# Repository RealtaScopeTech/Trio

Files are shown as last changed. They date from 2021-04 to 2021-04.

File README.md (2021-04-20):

# Trio
Realta Scope Tech: Trio Focuser

# What is it?

The REALTA Trio is a device that can control dew heaters, distribute 12 volt power and is an ASCOM compatible focuser. 

# Why did you make it?

The cost of some auxiliary astronomy equipment is crazy. I had no intention of paying $100 for a device the controls dew heaters via simple pulse width modulation, another $100 on a box that connects red and black wires to distribute 12v power and $200+ on a focuser controller. The cost saving plus the potential to learn something really intrigued me and the amount of information/free tools and general advice available to help people make things really inspired me, it's just astounding how useful the internet and open source/hardware have become. 

I also wanted to design something that fitted in a neat case as other maker options had a distinct DIY look to them, I wanted something that looked finished.

# License

Please feel free to make your own copies of the board/cases and ammend their design. Please give credit.

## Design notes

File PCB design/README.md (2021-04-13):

# PCB Design

The files used to design the PCB can be found in the KiCAD folder.

You may get issues with KiCAD not being able to find custom footprints and 3D models. We have placed all of those used within the KiCAD Extra's folder.

The "Production Files" folder contains all the files need to manufacture the PCB. It includes the Gerber files and a SMD position file and BOM file that can be used with JLCPCB to manufature a board with the SMD components included.

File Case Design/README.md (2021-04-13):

# Case Design

FreeCAD source files and STL's.

The parts are designed to be printed without supports. The motorhousing can be succesfully printed from the side which covers the stepper motors wires.

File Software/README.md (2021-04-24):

# Software
Realta Scope Tech: Trio Focuser

Windows Drivers => Contains drivers for the USB to Serial hardware found on many common Arduino Nano clones.

Select the folder that matches the name of the stepper driver board you are using in your Realta: Trio.

The installation process is the same for each driver.

# Nano software isntall

1) If needed install the driver for your Arduino's USB to Serial hardware.
2) Download the Arduino source code that matches your Arduino modela and the Stepper driver board you are using.
3) Download and install the Arduino IDE.
4) In the Arduino IDE install Adafruits AHT libraries.
5) Plug your Nano in
6) Open the Ardunio sketch source code you downloaded and compile/uploade it to the Nano.

# Windows app

1) Download the Trio.exe
2) Copy it somewhere where you can find it again!
3) Double click to run

# ASCOM driver.

1) Download the installer RealtaTrioASCOMSetup.exe, this is unsigned so Windows will probably think its a virus and warn you not to install it.

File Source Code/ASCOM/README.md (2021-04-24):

# ASCOM driver source code

Visual studio files

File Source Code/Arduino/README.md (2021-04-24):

# Arduniuo source code

Please select the approriate sketch for your stepper driver

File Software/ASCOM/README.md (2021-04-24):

# ASCOM

This ASCOM driver allows the focuser to be controlled with other ASCOM compliant software. 

It can not be used at the same time as the Windows desktop standalone app.

Dew controllers can be changed via the focusers settings menu.

Please note the driver is unsigned, Windows will therefore likely decide that it's a virus! You will need to select the option to install anyway.

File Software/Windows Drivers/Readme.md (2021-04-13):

# Windows Drivers
Drivers for Nano Clones USB to Serial hardware.

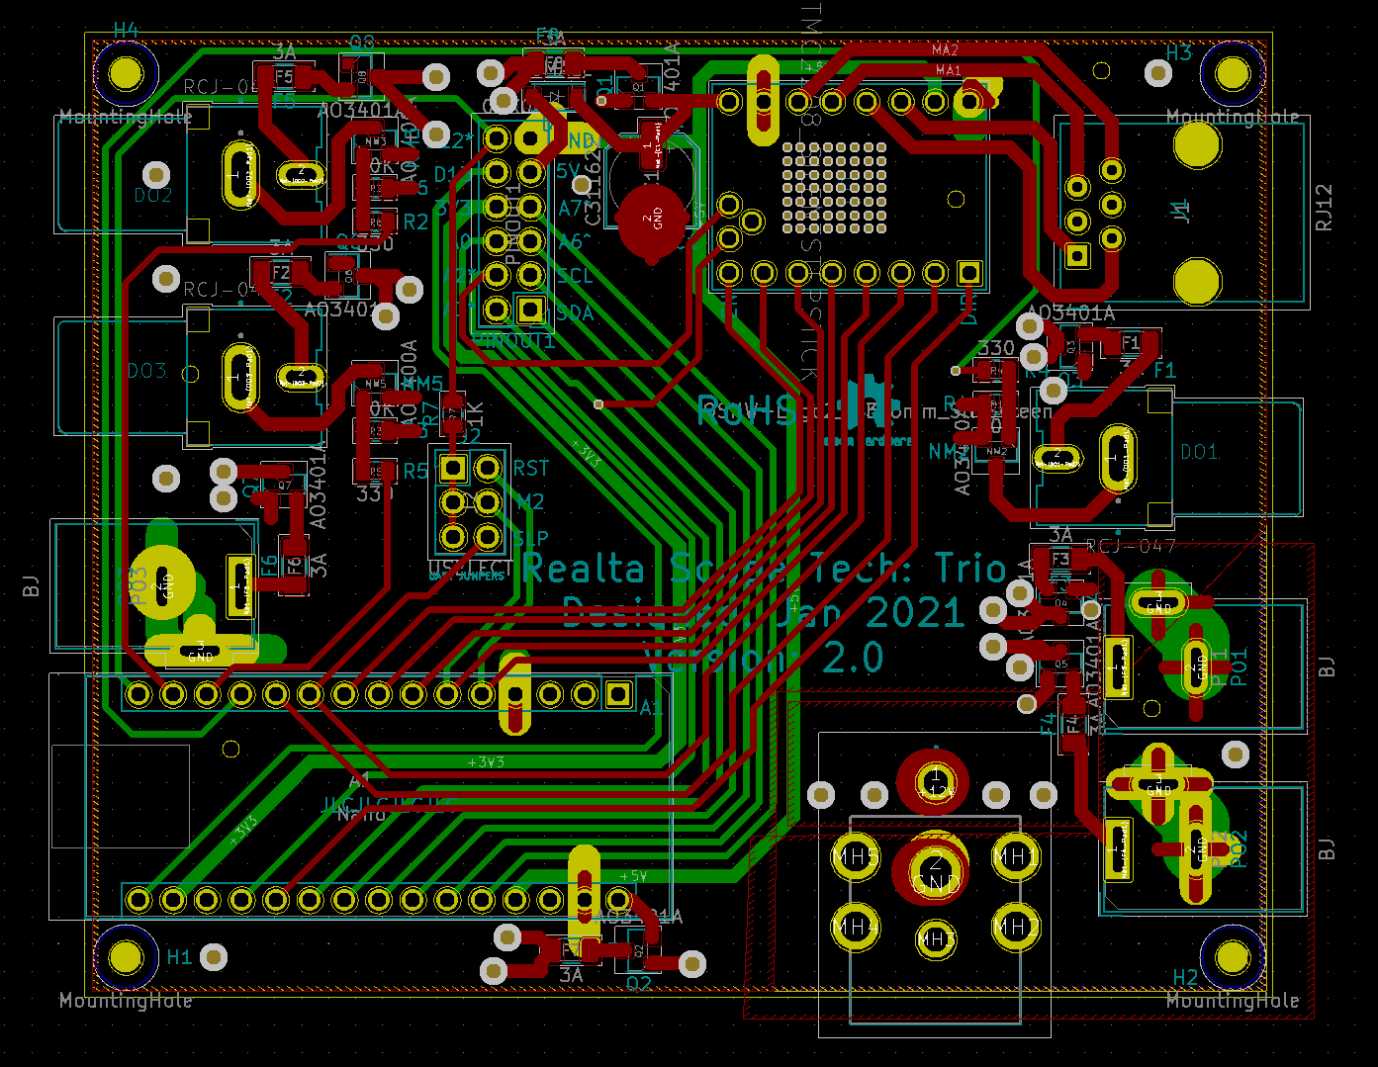
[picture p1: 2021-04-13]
PCB design/PCBLayout.png

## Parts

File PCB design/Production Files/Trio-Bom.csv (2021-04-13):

Comment | Designator | Footprint | LCSC
C311622 | C1 | Capacitor_SMD:CP_Elec_6.3x7.7 | C311622
DSMALL | D1 | Diode_SMD:D_SOD-123 | C8598
3A | F1,F2,F3,F4,F5,F6,F7,F8 | Fuse:Fuse_1206_3216Metric | C182445
AO3400A | NM2,NM3,NM5 | Package_TO_SOT_SMD:SOT-23 | C20917
AO3401A | Q1,Q2,Q3,Q4,Q5,Q6,Q7,Q8 | Package_TO_SOT_SMD:SOT-23 | C15127
10K | R1,R2,R3 | Resistor_SMD:R_0805_2012Metric | C17414
330 | R4,R5,R6 | Resistor_SMD:R_0805_2012Metric | C17630
1K | R7 | Resistor_SMD:R_0805_2012Metric | C17513

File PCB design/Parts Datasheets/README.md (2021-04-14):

# Parts Datasheets

Here you can find the data sheets of all the parts used in the Realta: Trio

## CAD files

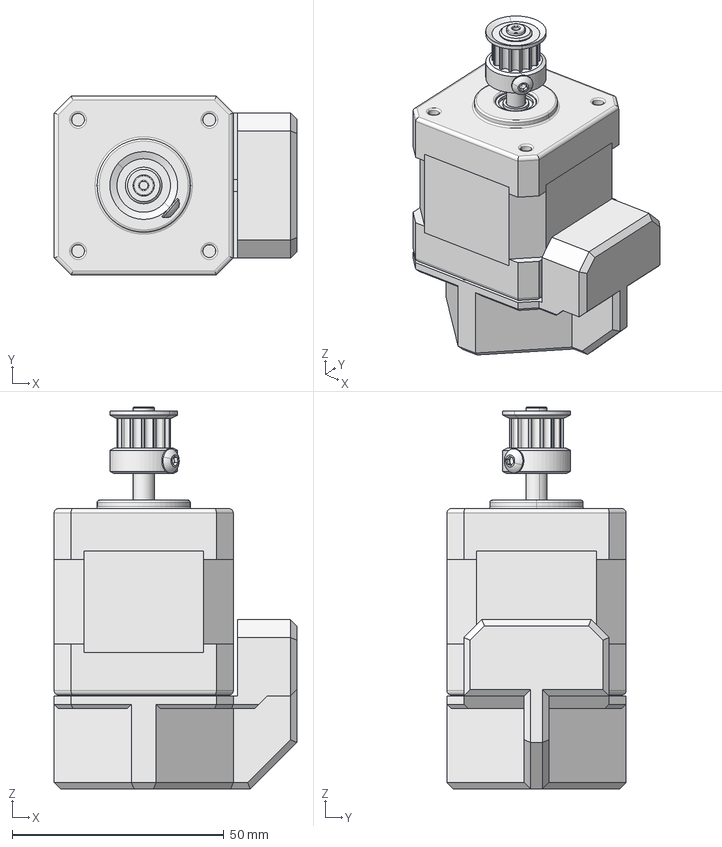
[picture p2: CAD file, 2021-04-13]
Case Design/FreeCAD/TrioMotorHousing.FCStd
57.3 x 42.3 x 90.2 mm
Base
Cuerpo
Tapa
pan cross head_am_B18.6.7M - M3 x 0.5 x 5 Type I Cross Recessed PHMS --5N
pan cross head_am_B18.6.7M - M3 x 0.5 x 5 Type I Cross Recessed PHMS --5N001
pan cross head_am_B18.6.7M - M3 x 0.5 x 5 Type I Cross Recessed PHMS --5N002
pan cross head_am_B18.6.7M - M3 x 0.5 x 5 Type I Cross Recessed PHMS --5N003
Eje
instrument ball bearing_68_am_AFBMA 12.1.4.1 - 0050-11 - 10,SI,NC,10_68
instrument ball bearing_68_am_AFBMA 12.1.4.1 - 0050-11 - 10,SI,NC,10_069
socket button head cap screw_am_B18.3.4M - 3 x 0.5 x 5 SBHCS --N
T5 Pulley

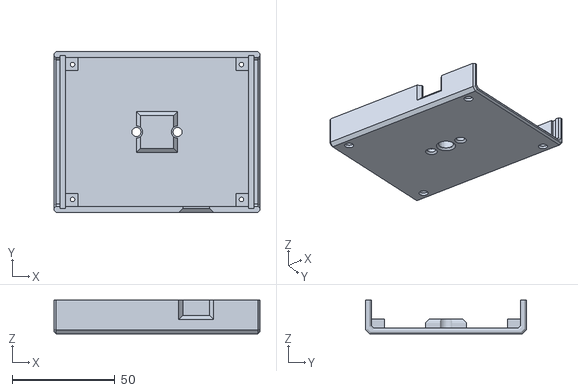
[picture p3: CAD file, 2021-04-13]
Case Design/STL/TrioLoweCase.stl
100.0 x 78.1 x 16.5

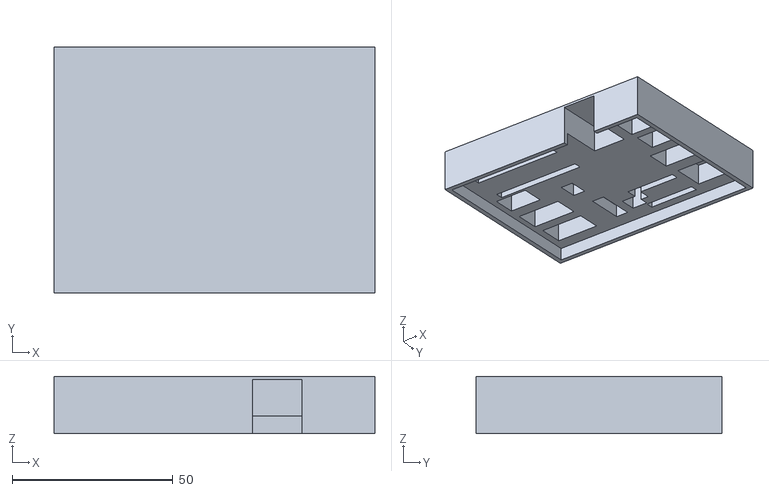
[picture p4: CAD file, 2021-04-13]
Case Design/STL/PCBSolderJig.stl
100.0 x 76.6 x 17.8

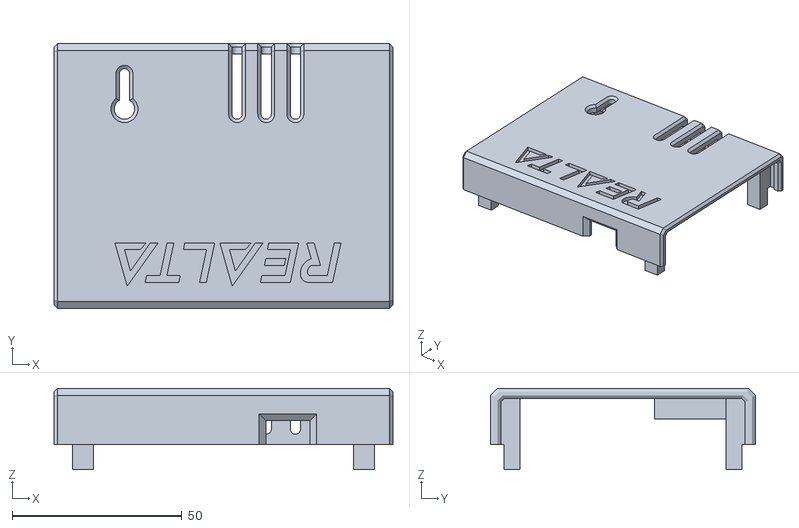
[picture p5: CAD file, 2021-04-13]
Case Design/STL/TrioUpperCase.stl
100.0 x 78.1 x 23.9

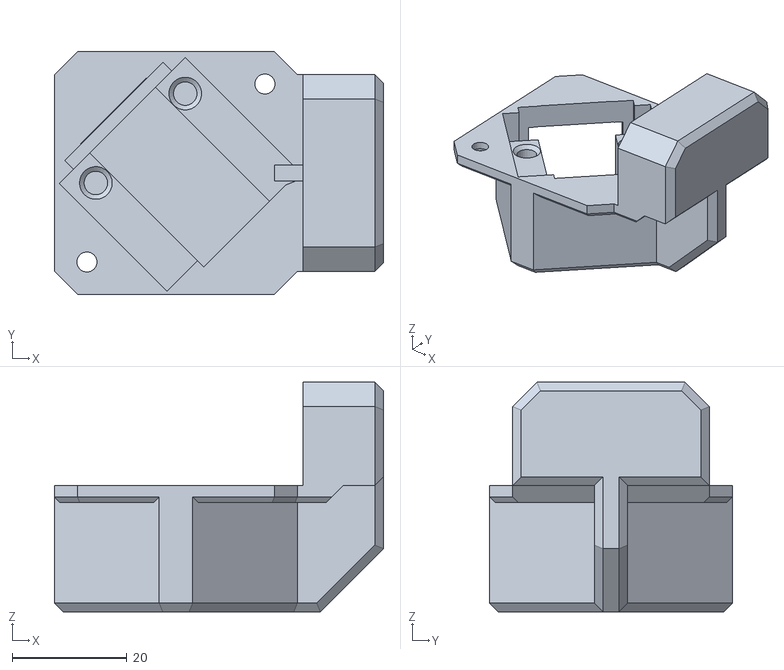
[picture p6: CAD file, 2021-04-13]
Case Design/STL/MotorHousing.stl
57.3 x 42.3 x 40.0

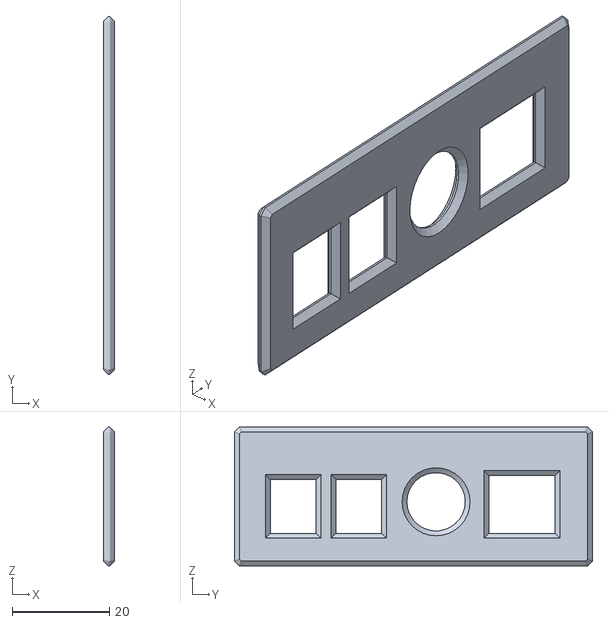
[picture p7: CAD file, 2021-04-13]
Case Design/STL/TrioFacePlateA.stl
2.32 x 73.7 x 28.6

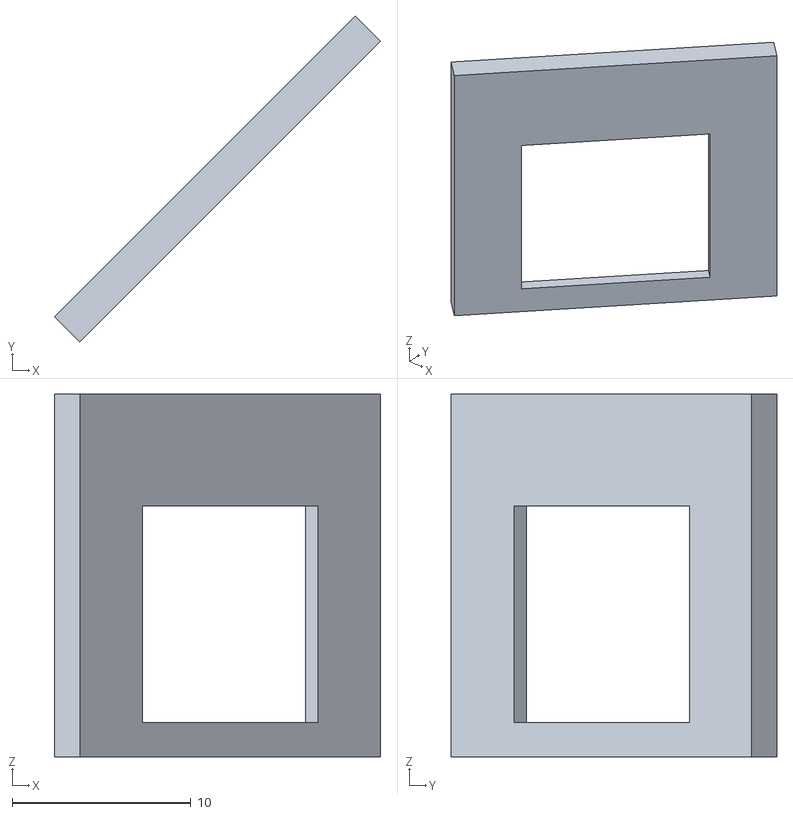
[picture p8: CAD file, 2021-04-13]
Case Design/STL/MotorFacePlate.stl
18.2 x 18.2 x 20.3

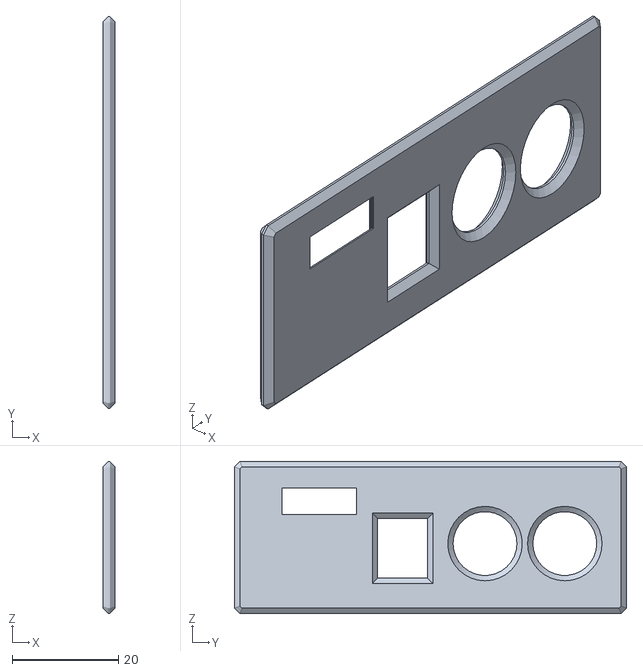
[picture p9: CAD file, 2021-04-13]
Case Design/STL/TrioFacePlateB.stl
2.32 x 73.7 x 28.6

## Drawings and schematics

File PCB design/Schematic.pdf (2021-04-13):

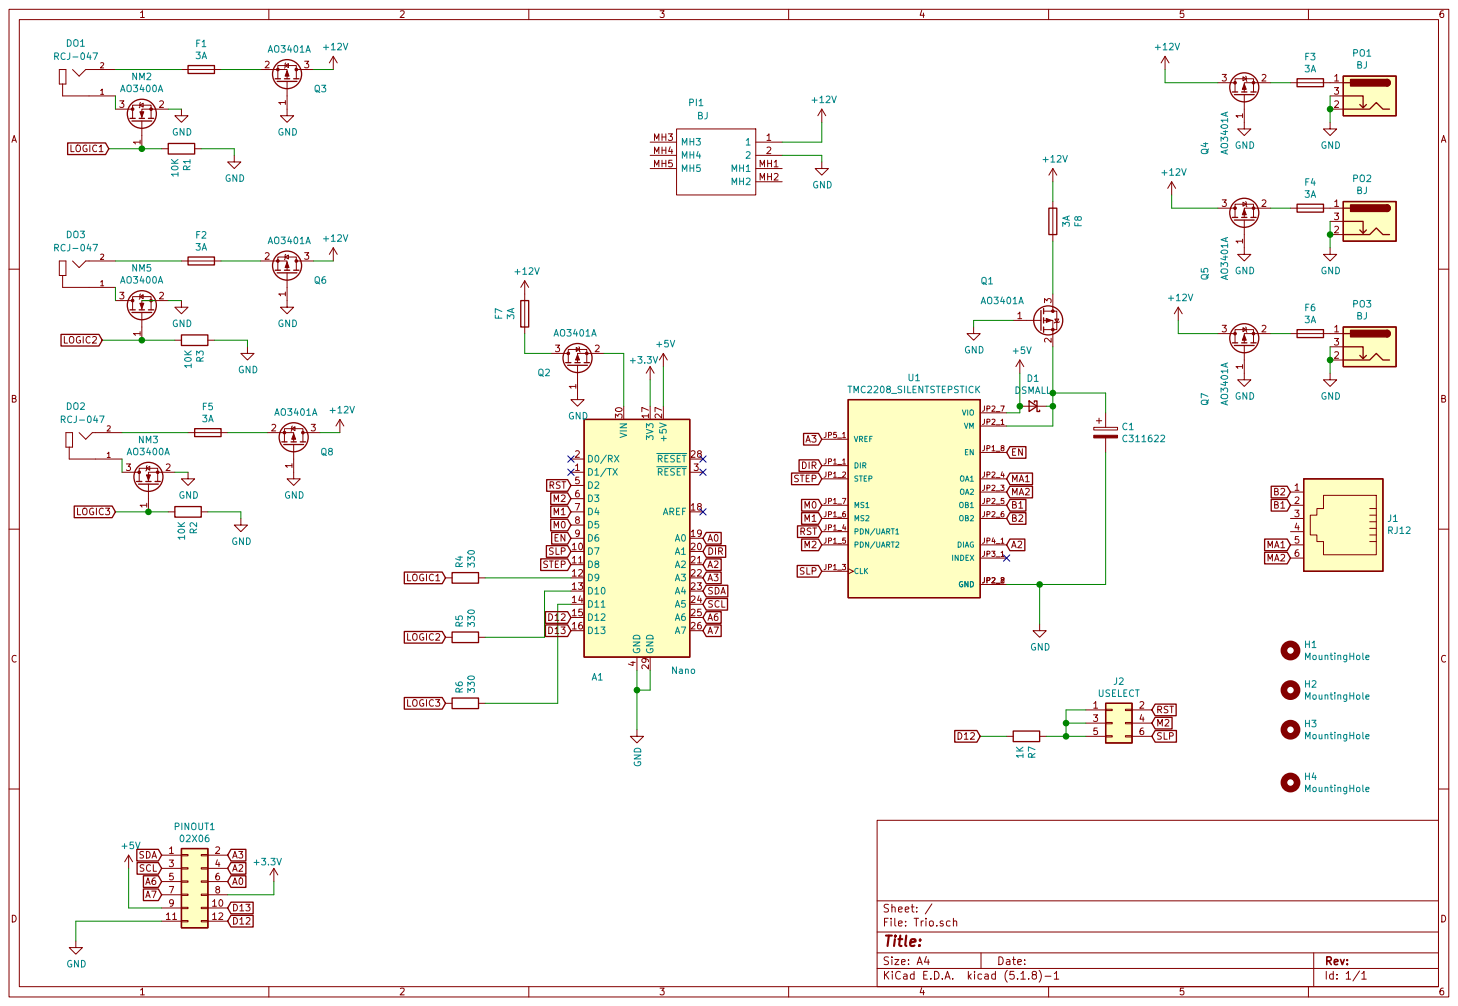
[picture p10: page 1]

Id: 1/1 Title: File: Trio.sch Sheet: / +3.3V

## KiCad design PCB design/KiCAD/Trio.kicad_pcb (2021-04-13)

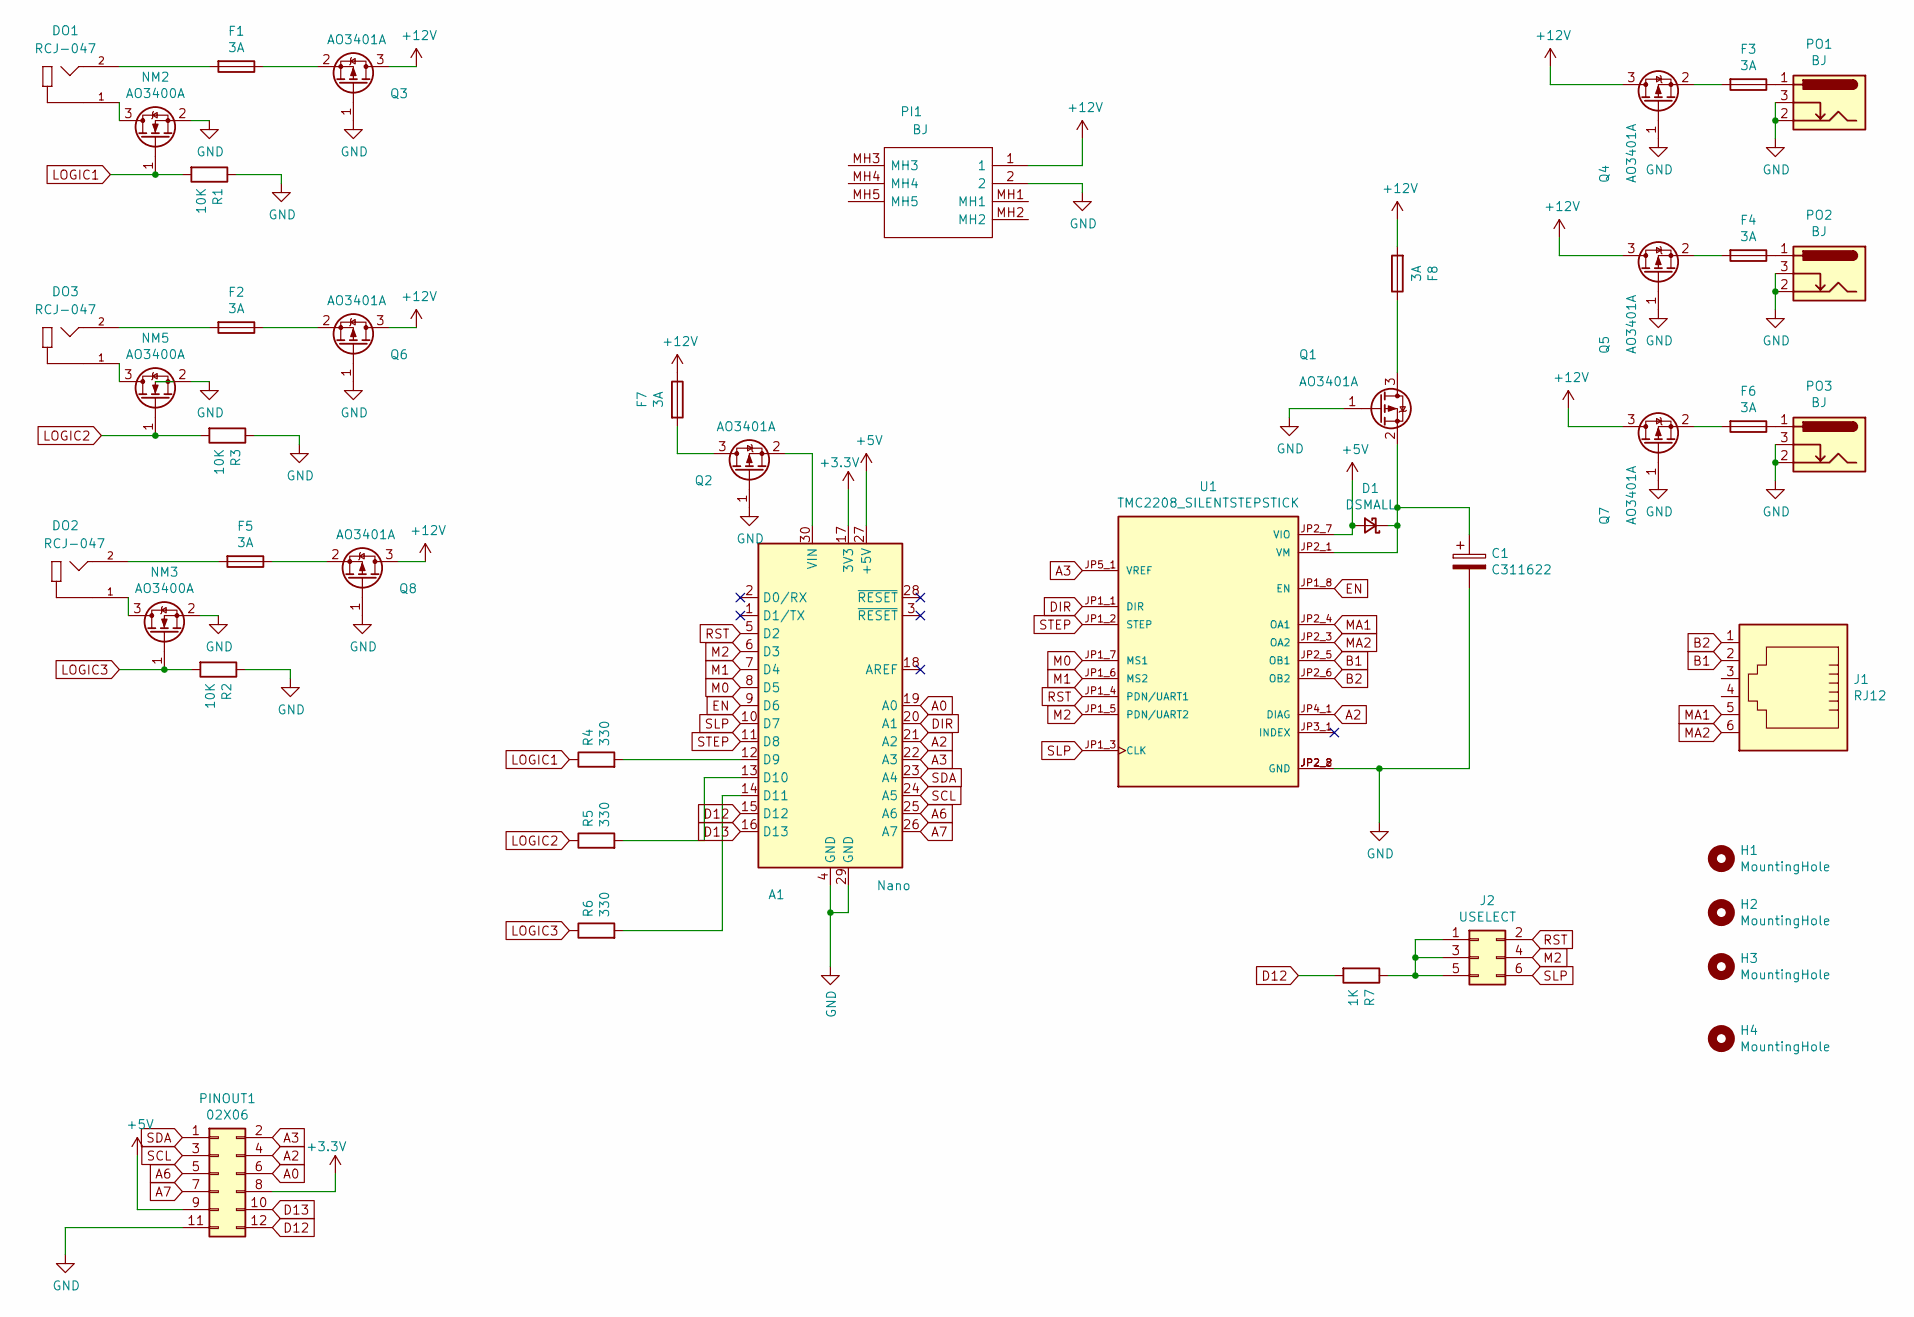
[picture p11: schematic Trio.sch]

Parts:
A1: Nano; Arduino_Nano
C1: C311622; CP_Elec_6.3x7.7; LCSC Part # C311622
D1: DSMALL; D_SOD-123; LCSC Part # C8598
DO1, DO2, DO3: RCJ-047; CUI_RCJ-047
F1, F2, F3, F4, F5, F6, F7, F8: 3A; Fuse_1206_3216Metric; LCSC Part # C182445
H1, H2, H3, H4: MountingHole; MountingHole_2.2mm_M2
J1: RJ12; RJ12_Amphenol_54601
J2: USELECT; PinHeader_2x03_P2.54mm_Vertical
NM2, NM3, NM5: AO3400A; SOT-23; LCSC Part # C20917
PI1: BJ; FC681495
PINOUT1: 02X06; PinHeader_2x06_P2.54mm_Vertical
PO1, PO2, PO3: BJ; BarrelJack_Wuerth_6941xx301002
Q1, Q2, Q3, Q4, Q5, Q6, Q7, Q8: AO3401A; SOT-23; LCSC Part # C15127
R1, R2, R3: 10K; R_0805_2012Metric; LCSC Part # C17414
R4, R5, R6: 330; R_0805_2012Metric; LCSC Part # C17630
R7: 1K; R_0805_2012Metric; LCSC Part # C17513
U1: TMC2208_SILENTSTEPSTICK; MODULE_TMC2208_SILENTSTEPSTICK; PARTREV v11

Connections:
+3V3: A1.17 (3V3), PINOUT1.8
+5V: A1.27 (+5V), D1.2 (A), PINOUT1.9, U1.JP2_7 (VIO)
+12V: F7.1, F8.2, PI1.1, Q3.3 (D), Q4.3 (D), Q5.3 (D), Q6.3 (D), Q7.3 (D), Q8.3 (D)
A0: A1.19 (A0), PINOUT1.6
A2: A1.21 (A2), PINOUT1.4, U1.JP4_1 (DIAG)
A3: A1.22 (A3), PINOUT1.2, U1.JP5_1 (VREF)
A6: A1.25 (A6), PINOUT1.5
A7: A1.26 (A7), PINOUT1.7
B1: J1.2, U1.JP2_5 (OB1)
B2: J1.1, U1.JP2_6 (OB2)
D12: A1.15 (D12), PINOUT1.12, R7.2
D13: A1.16 (D13), PINOUT1.10
DIR: A1.20 (A1), U1.JP1_1 (DIR)
EN: A1.9 (D6), U1.JP1_8 (EN)
GND: A1.4 (GND), A1.29 (GND), C1.2, NM2.2 (S), NM3.2 (S), NM5.2 (S), PI1.2, PINOUT1.11, PO1.2, PO1.3, PO2.2, PO2.3, PO3.2, PO3.3, Q1.1 (G), Q2.1 (G), Q3.1 (G), Q4.1 (G), Q5.1 (G), Q6.1 (G), Q7.1 (G), Q8.1 (G), R1.1, R2.1, R3.1, U1.JP2_2 (GND), U1.JP2_8 (GND)
LOGIC1: NM2.1 (G), R1.2, R4.1
LOGIC2: NM5.1 (G), R3.2, R5.1
LOGIC3: NM3.1 (G), R2.2, R6.1
M0: A1.8 (D5), U1.JP1_7 (MS1)
M1: A1.7 (D4), U1.JP1_6 (MS2)
M2: A1.6 (D3), J2.4, U1.JP1_5 (PDN/UART2)
MA1: J1.5, U1.JP2_4 (OA1)
MA2: J1.6, U1.JP2_3 (OA2)
unnamed: A1.12 (D9), R4.2
unnamed: A1.13 (D10), R5.2
unnamed: A1.14 (D11), R6.2
unnamed: A1.30 (VIN), Q2.2 (S)
unnamed: C1.1, D1.1 (K), Q1.2 (S), U1.JP2_1 (VM)
unnamed: DO1.1, NM2.3 (D)
unnamed: DO1.2, F1.2
unnamed: DO2.1, NM3.3 (D)
unnamed: DO2.2, F5.2
unnamed: DO3.1, NM5.3 (D)
unnamed: DO3.2, F2.2
unnamed: F1.1, Q3.2 (S)
unnamed: F2.1, Q6.2 (S)
unnamed: F3.1, PO1.1
unnamed: F3.2, Q4.2 (S)
unnamed: F4.1, PO2.1
unnamed: F4.2, Q5.2 (S)
unnamed: F5.1, Q8.2 (S)
unnamed: F6.1, PO3.1
unnamed: F6.2, Q7.2 (S)
unnamed: F7.2, Q2.3 (D)
unnamed: F8.1, Q1.3 (D)
unnamed: J2.1, J2.3, J2.5, R7.1
RST: A1.5 (D2), J2.2, U1.JP1_4 (PDN/UART1)
SCL: A1.24 (A5), PINOUT1.3
SDA: A1.23 (A4), PINOUT1.1
SLP: A1.10 (D7), J2.6, U1.JP1_3 (CLK)
STEP: A1.11 (D8), U1.JP1_2 (STEP)

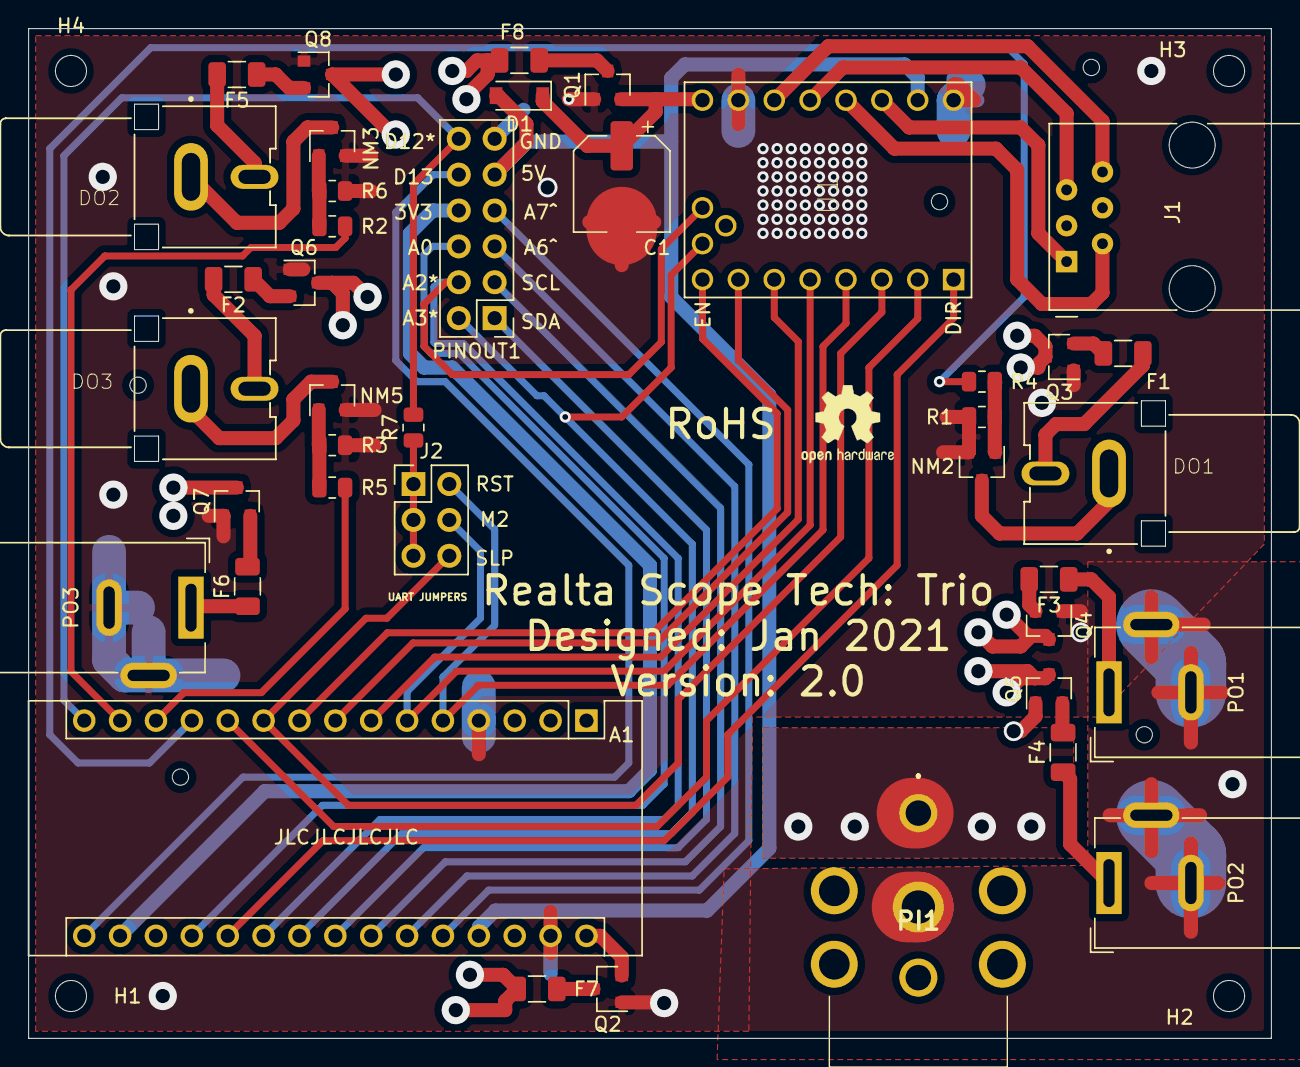
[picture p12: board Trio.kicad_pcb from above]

Board: 4 copper layers, 88.0 x 71.5 mm, 44 parts (0 on the bottom side), 51 nets.

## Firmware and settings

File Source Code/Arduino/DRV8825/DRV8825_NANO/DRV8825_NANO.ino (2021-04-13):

// Realta: Súil a Trí
#include <EEPROM.h>
#include <Arduino.h>
#include <Adafruit_AHTX0.h>
#include "MyData.h"
#include "MyEPROM.h"
#include "MyDew.h"
#include "MyFocus.h"
#include "MyTemp.h"
#include "MySerial.h"

void setup() {
  // turn the serial port on
  // code in MySerial.h
  P_INIT_SERIAL_PORT();
  
  // Set output pins
  // See DataStructure for pin mapping
  // Code in MyData.h
  P_SET_OUTPUT_PINS();
  
  //Read last saved dew status
  // Code in MyEPROM.h
  READ_EPROM_DEW();
  
  //Read last saved dew status
  // Code in MyEPROM.h
  READ_EPROM_FOCUSER();
  //Set PWM values to zero
  //We do not want these to come on unless user asks for it
  V_DEW_LOCKED = true;
  V_IS_MOVING = false;
  V_STEPS_TO_MAKE = 0;

  // SET DEFAULT STEPPING MODE REFERENCES
  P_SET_STEPPING_MODES();

  // SET SLEEP AND RESET HIGH
  pinMode(2, OUTPUT);
  pinMode(7, OUTPUT);
  digitalWrite(2, HIGH );
  digitalWrite(7, HIGH );

  // UPDATE STEPPING PINS TO SAVED VALUES
  P_UPDATE_STEPPER_PINS();

  // Try to start AHT20
  P_CHECK_SENSOR_EXISTS();

  // Read temp offset
  READ_EPROM_TEMP_OFFSET();
  
}


//////////////////////////////////////////////////////////////////////
//////////////////////////////////////////////////////////////////////
//////////////////////////////////////////////////////////////////////
//////////////////////////////////////////////////////////////////////


void loop() {
  
  ////////////////////////////////
  //
  // Check and read serial port
  //
  ///////////////////////////////

  // This procedure reads latest serial port 
  // value and decides what to do with it
  // it will keep adding chars to V_SERIAL_TEXT until it gets to a line feed
  // then send the command on to processing
  // Code in MySerial.h
  P_PROCESS_SERIAL_PORT ();

  if (V_IS_MOVING)
  {
    P_STEP ();
  }

  // Not sure if I need to keep setting the PWM pins every loop.
  // Code in MyDew.h
  P_SET_PWM_PINS();

}

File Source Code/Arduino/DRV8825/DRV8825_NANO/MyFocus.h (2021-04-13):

/*
byte DEW_0_PIN = 9;       //PWM PULSES
byte DEW_1_PIN = 10;      //PWM PULSES
byte DEW_2_PIN = 11;      //PWM PULSES
byte STEP_DIR_PIN = 3;    //SETS DIRECTION
byte STEP_STEP_PIN = 4;   //TELLS MOTOR TO MOVE
byte STEP_ENABLE_PIN = 8; //ENABLES POWER TO MOTOR
byte STEP_M3_PIN = 7;     //FOR SETTING STEP SIZE
byte STEP_M2_PIN = 6;     //FOR SETTING STEP SIZE
byte STEP_M1_PIN = 5;     //FOR SETTING STEP SIZE

struct FOCUSER_STATUS {
  int  V_CURRENT_POSITION;
  byte V_STEP_MODE;
  int  V_MAX_STEPS;
  byte V_POWER_HOLD;
  byte V_DIRECTTION;
  byte V_STEPPER_SPEED;
};

*/

// STEPPER CONTROL

void P_UPDATE_STEPPER_PINS()
{
digitalWrite(STEP_DIR_PIN, S_MY_FOCUSER_STATUS.V_DIRECTTION);
digitalWrite(STEP_ENABLE_PIN, S_MY_FOCUSER_STATUS.V_POWER_HOLD);
digitalWrite(STEP_M1_PIN, STEPPING_MODE[S_MY_FOCUSER_STATUS.V_STEP_MODE].M1_STATE );
digitalWrite(STEP_M2_PIN, STEPPING_MODE[S_MY_FOCUSER_STATUS.V_STEP_MODE].M2_STATE );
digitalWrite(STEP_M3_PIN, STEPPING_MODE[S_MY_FOCUSER_STATUS.V_STEP_MODE].M3_STATE );
}

// SERIAL LETTER 'FOCUSER_GET_STATUS': GET_FOCUSER_STATUS
//  returns
//  V_CURRENT_POSITION, V_STEP_MODE, V_MAX_STEPS, V_POWER_HOLD, V_DIRECTTION, V_STEPPER_SPEED;
//  return should look like GET_STEPPER_STATUS|5000, 1, 10000, 0, 0, 1

// SERIAL LETTER 'D': SET_STEPPER_STATUS
// sends new V_CURRENT_POSITION, V_STEP_MODE, V_MAX_STEPS, V_POWER_HOLD, V_DIRECTTION, V_STEPPER_SPEED;

// SERIAL 'FOCUSER_MOVE': MOVE_NUMBER_OF_STEPS
void P_OUTPUT_FOCUSER_STATUS ()
{
  V_SERIAL_OUT ="";

   V_SERIAL_OUT = "FOCUSER_STATUS";
   V_SERIAL_OUT = V_SERIAL_OUT + "|";
   V_SERIAL_OUT = V_SERIAL_OUT + S_MY_FOCUSER_STATUS.V_CURRENT_POSITION + "," ; 
   V_SERIAL_OUT = V_SERIAL_OUT + S_MY_FOCUSER_STATUS.V_STEP_MODE + ","; 
   V_SERIAL_OUT = V_SERIAL_OUT + S_MY_FOCUSER_STATUS.V_MAX_STEPS + "," ;
   V_SERIAL_OUT = V_SERIAL_OUT + S_MY_FOCUSER_STATUS.V_POWER_HOLD + "," ;
   V_SERIAL_OUT = V_SERIAL_OUT + S_MY_FOCUSER_STATUS.V_DIRECTTION + "," ;
   V_SERIAL_OUT = V_SERIAL_OUT + S_MY_FOCUSER_STATUS.V_STEPPER_SPEED + ",";
   V_SERIAL_OUT = V_SERIAL_OUT + S_MY_FOCUSER_STATUS.V_STEPPER_WAIT;
   Serial.println(V_SERIAL_OUT);
   
};  

void P_STEP ()
{
    if(V_STEPS_TO_MAKE != 0)
    {
    // We will update stepper pins to users last settings
    P_UPDATE_STEPPER_PINS();

    // We will ignore enable flag because we do actually want to move
    digitalWrite(STEP_ENABLE_PIN, LOW);

   // Reverse direction if negative steps
    if (V_STEPS_TO_MAKE < 0)
    {
    if(S_MY_FOCUSER_STATUS.V_DIRECTTION == 1)
      {
        digitalWrite(STEP_DIR_PIN, 0);
      }
      else
      {
        digitalWrite(STEP_DIR_PIN, 1);
      }
    }
    
    delay(S_MY_FOCUSER_STATUS.V_STEPPER_SPEED); // Wait per user speed delay
    // Focuser moves only when stop pin changes from high to low
    digitalWrite(STEP_STEP_PIN, LOW);
    digitalWrite(STEP_STEP_PIN, HIGH) ;
      
    // Wait for it   
    delay(S_MY_FOCUSER_STATUS.V_STEPPER_WAIT);  

    if (V_STEPS_TO_MAKE < 0)
    {
    S_MY_FOCUSER_STATUS.V_CURRENT_POSITION = S_MY_FOCUSER_STATUS.V_CURRENT_POSITION - 1;
    V_STEPS_TO_MAKE =  V_STEPS_TO_MAKE + 1;
    }
    else
    {
    S_MY_FOCUSER_STATUS.V_CURRENT_POSITION = S_MY_FOCUSER_STATUS.V_CURRENT_POSITION + 1;
    V_STEPS_TO_MAKE =  V_STEPS_TO_MAKE - 1;   
    }
    }

    // Output progress
    if (V_STEPS_TO_MAKE % 100 == 0)
    {
    Serial.print("MOVING|"); Serial.println(V_STEPS_TO_MAKE);
    }


    if (V_STEPS_TO_MAKE==0)
    {
    V_IS_MOVING = false;
    SAVE_EPROM_FOCUSER();
    P_OUTPUT_FOCUSER_STATUS ();
    }
    
    // We will update stepper pins back to user settings 
    P_UPDATE_STEPPER_PINS();
    
}


void P_MOVE_FOCUSER ()
{
   // We expect parameter containing number of steps
   // throw error back if we don't have any
   if(!V_HAS_PARAMS) 
   {
      Serial.println ("ERROR|NO PARAMATERS");
   } 
   if(V_HAS_PARAMS) 
   {
    // Dig out number of steps to make from parameter list, should only be one entry
    V_CHAR_STEPS_TO_MAKE = V_PARAMS.substring(1);
    V_STEPS_TO_MAKE_TEMP = V_CHAR_STEPS_TO_MAKE.toInt();


    // Added check to make sure don't move past 0 and S_MY_FOCUSER_STATUS.V_MAX_STEPS
    V_NEW_CURRENT_POSITION = S_MY_FOCUSER_STATUS.V_CURRENT_POSITION + V_STEPS_TO_MAKE_TEMP;

    V_CORRECTED_POSITION =  max(min(V_NEW_CURRENT_POSITION, S_MY_FOCUSER_STATUS.V_MAX_STEPS),0);
     
    V_STEPS_TO_MAKE   = V_CORRECTED_POSITION - S_MY_FOCUSER_STATUS.V_CURRENT_POSITION;
    
    if (V_STEPS_TO_MAKE != 0)
    {
     V_IS_MOVING = true;
    }

    if (V_STEPS_TO_MAKE == 0)
    {
     V_IS_MOVING = false;
     P_OUTPUT_FOCUSER_STATUS ();
    }
  } 
}

void P_FOCUSER_SET_PARAM ()
{
   // Expecting a ton of values
   if(!V_HAS_PARAMS) 
   {
   Serial.println ("ERROR|NO PARAMATERS");
   }

   // if it does have some we will dig em out
   if(V_HAS_PARAMS)
   {
    
    S_TEMP_FOCUSER_STATUS.V_CURRENT_POSITION = F_GET_VALUE(V_PARAMS.substring(1),',',0).toInt(); 
    S_TEMP_FOCUSER_STATUS.V_STEP_MODE        = F_GET_VALUE(V_PARAMS.substring(1),',',1).toInt(); 
    S_TEMP_FOCUSER_STATUS.V_MAX_STEPS        = F_GET_VALUE(V_PARAMS.substring(1),',',2).toInt();
    S_TEMP_FOCUSER_STATUS.V_POWER_HOLD       = F_GET_VALUE(V_PARAMS.substring(1),',',3).toInt();
    S_TEMP_FOCUSER_STATUS.V_DIRECTTION       = F_GET_VALUE(V_PARAMS.substring(1),',',4).toInt();
    S_TEMP_FOCUSER_STATUS.V_STEPPER_SPEED    = F_GET_VALUE(V_PARAMS.substring(1),',',5).toInt();
    S_TEMP_FOCUSER_STATUS.V_STEPPER_WAIT     = F_GET_VALUE(V_PARAMS.substring(1),',',6).toInt();




    // Check each value is in range.
    // Don't rely on front end
    V_PARAM_ERROR_TEXT = "";
    V_PARAM_ERROR = false;
    
    if (S_TEMP_FOCUSER_STATUS.V_CURRENT_POSITION < 0) {
        V_PARAM_ERROR_TEXT = V_PARAM_ERROR_TEXT + "|CURRENT_POSTION_LESS_THAN_ZERO";
        V_PARAM_ERROR = true;
    }

    if (S_TEMP_FOCUSER_STATUS.V_CURRENT_POSITION > S_TEMP_FOCUSER_STATUS.V_MAX_STEPS) {
        V_PARAM_ERROR_TEXT = V_PARAM_ERROR_TEXT + "|CURRENT_POSTION_GREATER_THAN_MAX";
        V_PARAM_ERROR = true;
    }

    if (S_TEMP_FOCUSER_STATUS.V_STEP_MODE < 0 || S_TEMP_FOCUSER_STATUS.V_STEP_MODE > 5 ) {
        V_PARAM_ERROR_TEXT = V_PARAM_ERROR_TEXT + "|STEP_MODE_OUT_OF_RANGE";
        V_PARAM_ERROR = true;
    }
    
    if (S_TEMP_FOCUSER_STATUS.V_MAX_STEPS < 0) {
        V_PARAM_ERROR_TEXT = V_PARAM_ERROR_TEXT + "|MAX_STEPS_LESS_THAN_ZERO";
        V_PARAM_ERROR = true;
    }

    if (S_TEMP_FOCUSER_STATUS.V_POWER_HOLD < 0 || S_TEMP_FOCUSER_STATUS.V_POWER_HOLD > 1 ) {
        V_PARAM_ERROR_TEXT = V_PARAM_ERROR_TEXT + "|POWER_HOLD_OUT_OF_RANGE";
        V_PARAM_ERROR = true;
    }

    if (S_TEMP_FOCUSER_STATUS.V_DIRECTTION < 0 || S_TEMP_FOCUSER_STATUS.V_DIRECTTION > 1) {
        V_PARAM_ERROR_TEXT = V_PARAM_ERROR_TEXT + "|DIRECTION_OUT_OF_RANGE";
        V_PARAM_ERROR = true;
    }
    
    if (S_TEMP_FOCUSER_STATUS.V_STEPPER_SPEED < 0) {
        V_PARAM_ERROR_TEXT = V_PARAM_ERROR_TEXT + "|STEPPER_SPEED_LESS_THAN_ZERO";
        V_PARAM_ERROR = true;
    }
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
